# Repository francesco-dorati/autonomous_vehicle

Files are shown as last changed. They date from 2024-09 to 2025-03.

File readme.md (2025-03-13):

# Autonomous Mobile Robot
<!-- [manual interface](./img/manual_interface.png) -->
## Introduction
The aim of this project is to build an autonomous mobile robot capable of **localization**, **mapping** and **autonomous planning** in real-time.
This project is still under development.

### Main Components
- Raspberry Pi 
- Arduino nano
- Arduino RP2040 Connect
- RP Lidar
- [Full components list...](docs/compnents_list.md)

## Software Details
### Program Structure
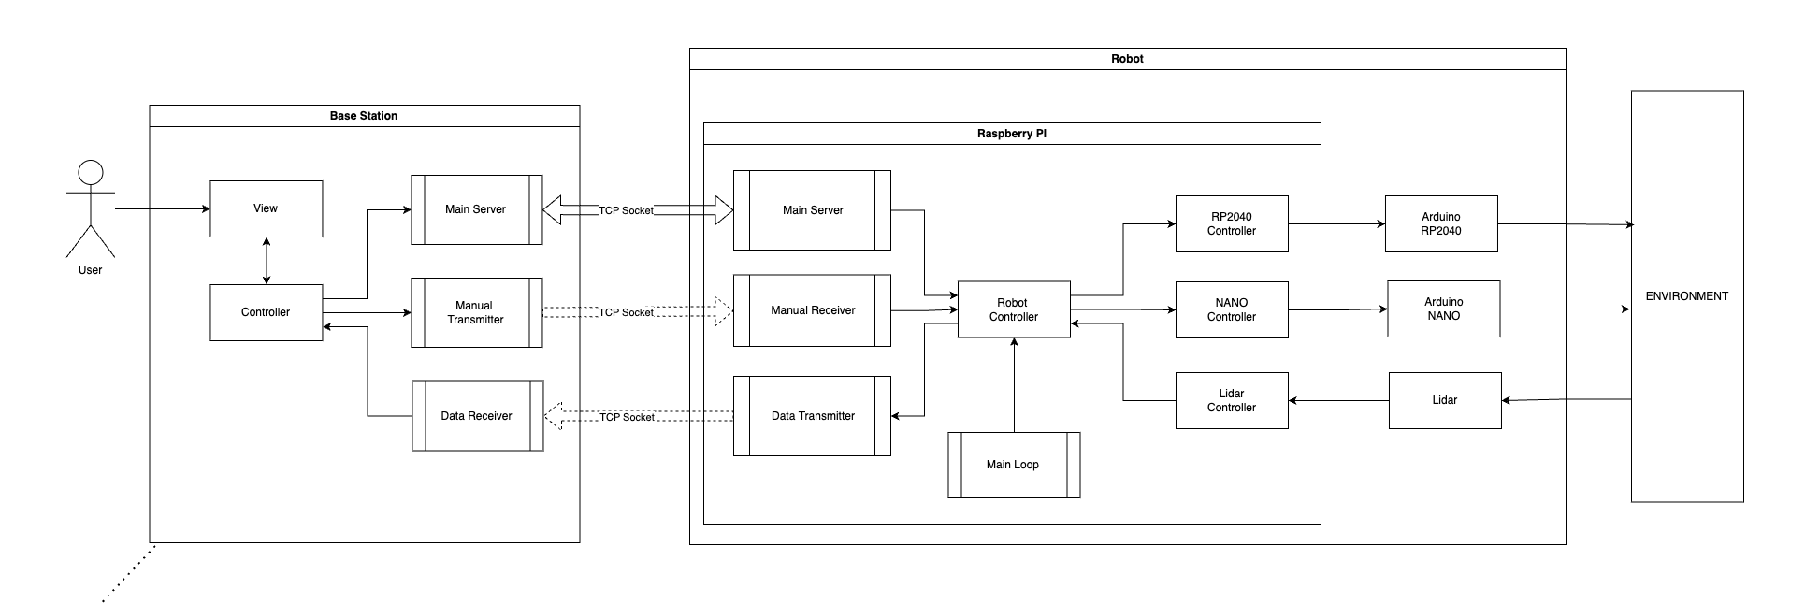
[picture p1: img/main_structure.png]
program structure


#### Robot Controller  (RaspberryPi)
Main controller of the robot, handles main logic and runs the control loop.  

##### Control Loop [4/5 Hz]
The control loop is responsible for the continuous operation of the robot, handling perception, planning, and control tasks.

1. **Perception**
    1. **State Prediction**:
        - Retreaves odometry data from Arduino RP2040
        - Uses an **Extended Kalman Filter (EKF)** to predict the new state (x, y, th, v, w).
    2. **Visual Odometry**:
        - Processes data from the Lidar to create a local map.
        - Uses **ICP** to compute map transformation.
    3. **State Update**:
        - Refines the predicted state using visual odometry data.
    4. **Mapping**:
         - If mapping is enabled, **expands the global map** with lidar data.

2. **Planning**
    1. **Control Commands**: Depending on the control type (position or velocity), sends appropriate commands to the RP2040 to move the robot.

The loop runs continuously at a specified interval, ensuring the robot can navigate and map its environment in real-time.  
[[robot.py](src/raspberry_pi/robot/robot.py)]

#### Motor Controller (Arduino RP2040) [50 Hz]
Handles velocity control of motors and wheel odomtery.
Receives commands from the Robot Controller and translates them into motor actions using a PID control.
Sends encoder data to the Robot Controller each loop.
The Arduino RP2040 communicates with the Raspberry Pi via UART2.
[[arduino code](src/arduino_rp2040/main.ino),  [raspberrypi driver](src/raspberrypi/rp2040.py)]

<!-- #### Motor Controller (Arduino Nano)

[[arduino code](src/nano/main.ino),  [raspberrypi driver](src/raspberrypi/nano.py)]
```
NANO LOOP (50Hz):
- read from serial
- set motor powers
``` -->
#### Developer Console (Client)
Graphical interface to allow the end-user to remotely control the robot while receiving camera streaming and sensors feedback.
Connects to RaspberryPI with multiple socket connections.

<!--
### Interfaces & Connections

#### Sockets (DevConsole <-> RaspberryPI):
- main: TCP (req/res)
- manual: UDP (bidirect)
- camera: UDP (monodirect)
```
MAIN
console (request) ->  raspberrypi (response)
"P"          ->    "P <battery_v>"             // Ping
"M <0/1>"    ->    "OK <manual_port>"          // Manual Start/Stop
"C <0/1>"    ->    "OK <camera_port>"          // Camera Start/Stop
"E"          ->    "OK"                        // Close Connection

MANUAL
console: "<boost> <x> <y>"                   // commands (boost, x, y ∈ [-1,0,1])
raspberrypi: "D <fl> <fr> <rl> <rr>",        // obstacle distance (cm, cm, cm, cm)
             "E <vx> <vt> <x> <y> <theta>",  // encoders odometry (cm/s, deg/s, cm, cm, deg)
``` ->
<- 
#### Serial:
- arduino nano: UART0
- arduino rp2040: UART2 -->

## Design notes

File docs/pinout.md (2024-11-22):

### RASPBERRYPI

### ARDUINO RRP2040
 - TX -> GPIO1 RPI 
 - RX -> GPIO0 RPI 
 - D2 -> IN1  (shifter)
 - D3 -> IN2 (shifter)
 - D4 -> ENA (shifter)
 - D5 -> ENB (shifter)
 - D6 -> IN3 (shifter)
 - D7 -> IN4 (shifter)
 - D8 -> RB Encoder
 - D9 -> RA Encoder
 - D10 -> LB Encoder
 - D11 -> LA Encoder

### ARDUINO NANO
 - TX -> RX RPI (shifter)
 - RX -> TX RPI (shifter)
 - A0 -> Bettery Reader
 - D2 -> FL trig
 - D3 -> FL echo
 - D4 -> FR trig
 - D5 -> FR echo
 - D6 -> RL trig
 - D7 -> RL echo
 - D8 -> RR trig
 - D9 -> RR echo

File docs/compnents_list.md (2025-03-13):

## Components:
### Power:
 - Battery 12v 2200mAh 
 - DCDC Converter 12v-5v 15W 
 - Fuse 7.5A 
 - Power Switch

### Controllers:
 - Raspberry PI
 - Arduino RP2040 Connect
 - Arduino NANO

### Motors:
 - L298N Motor Driver
 - DC Motor 12v 170rpm (x2)
    - current: 60mA free, 450mA load, 1300mA stall 

### Sensors:
 - Slamtec RPLIDAR C1 
 - Ultrasonic Sensor HCSR04 (x4)
 - Digital Camera OV5647, 160° 5MP

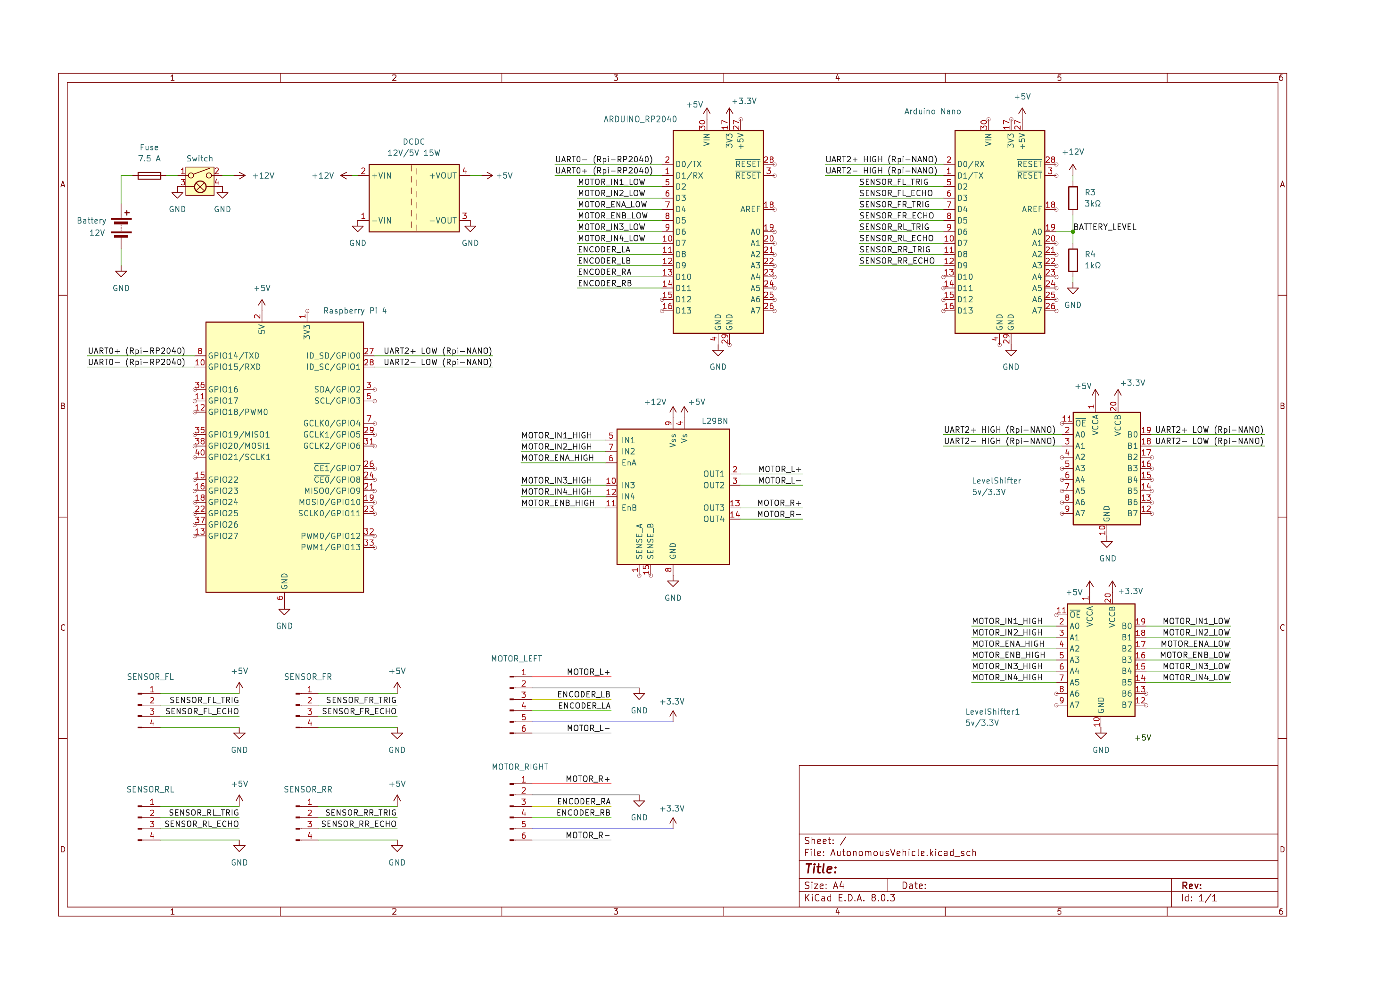
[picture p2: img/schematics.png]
schematics


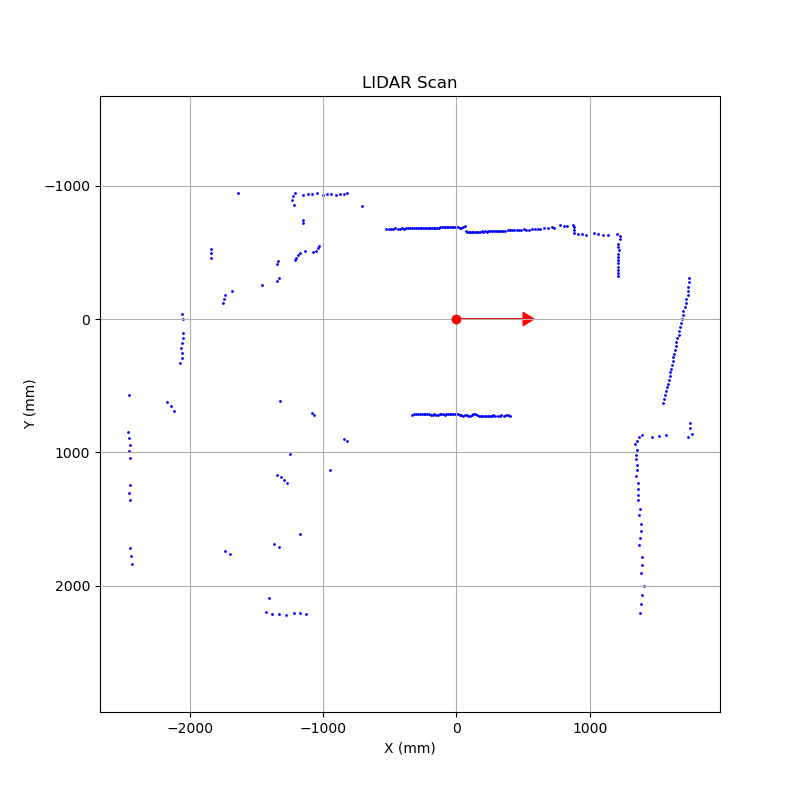
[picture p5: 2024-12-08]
img/local0.png

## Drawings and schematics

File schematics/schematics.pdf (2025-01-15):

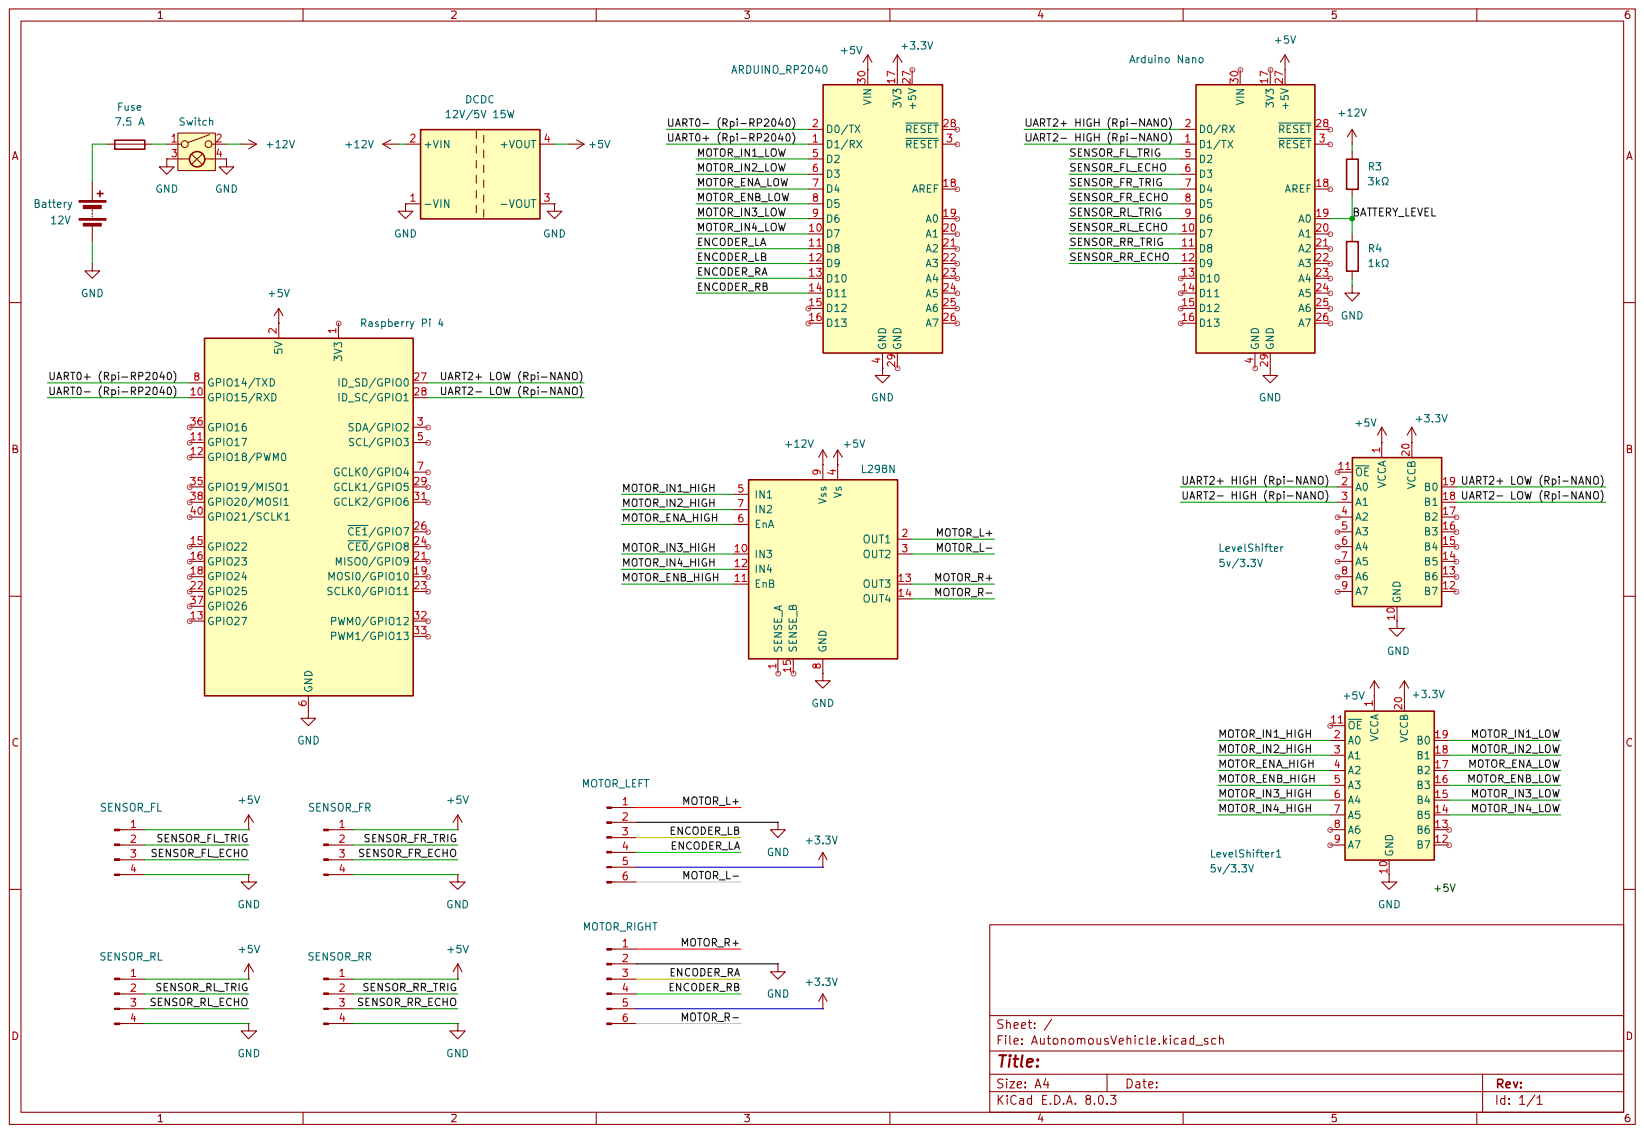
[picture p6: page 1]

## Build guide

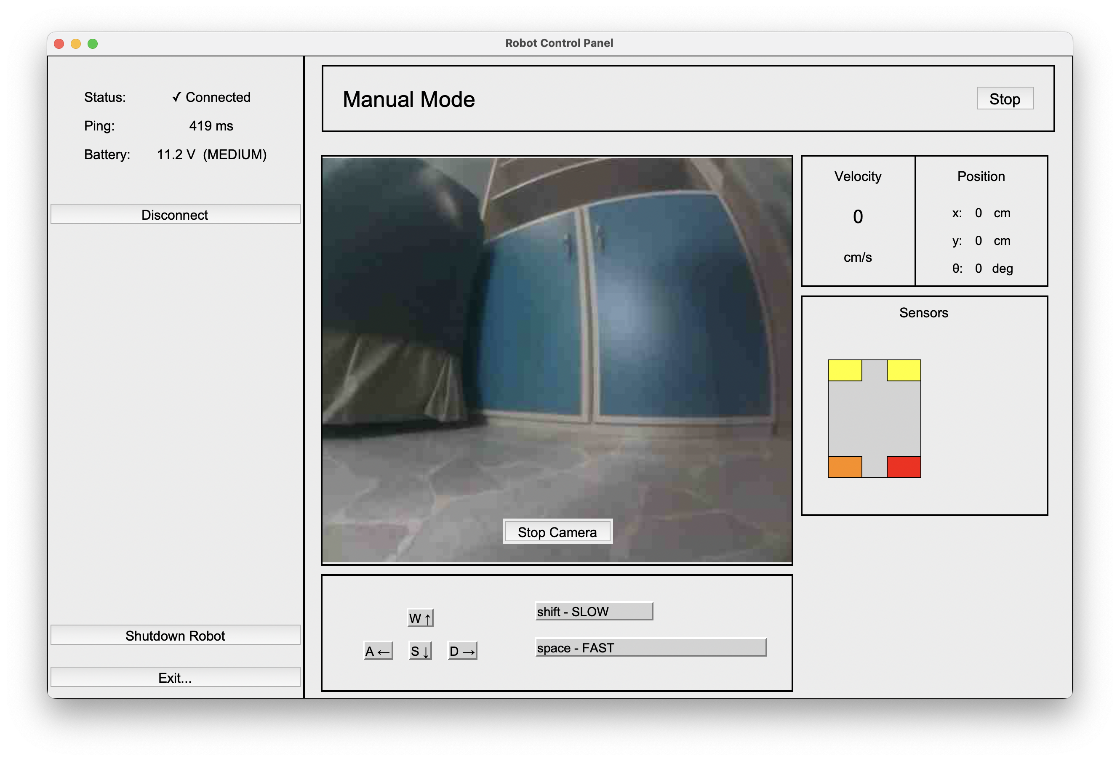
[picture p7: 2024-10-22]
img/manual_interface.png

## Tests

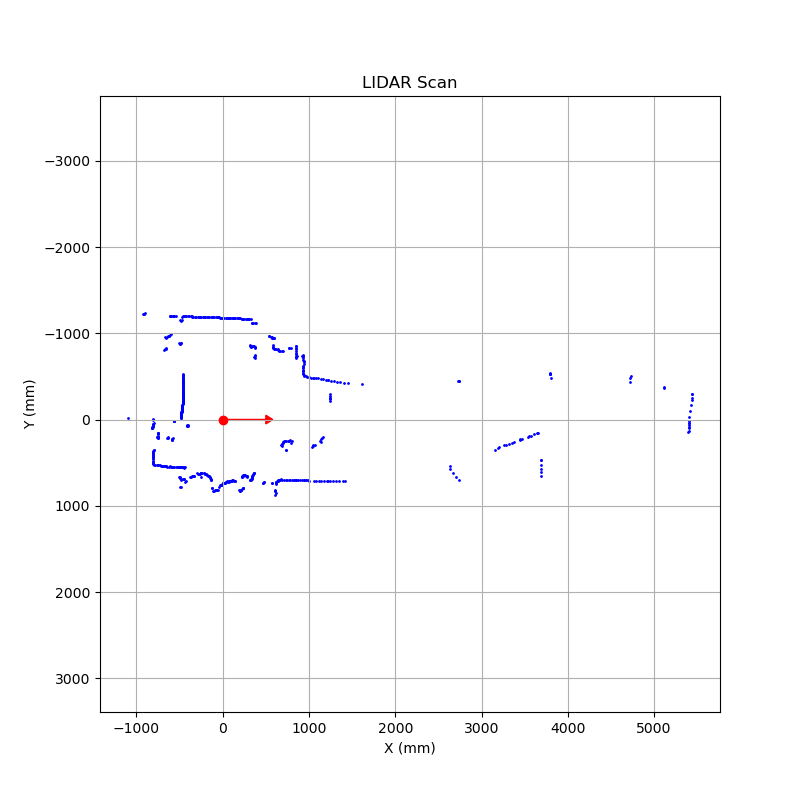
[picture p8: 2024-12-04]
img/test3.png

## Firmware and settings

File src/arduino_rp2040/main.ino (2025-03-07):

#include <Arduino.h>
#include <WiFiNINA.h>
#include <math.h>
#include <PID_v1.h>

/*    
    Motor Controller 
    Handles motor control, path following and encoders odometry calculations
    When not in STALL sends odometry data via serial

    INPUTS (Serial1 115200) 
    ALL INPUTS ENDS WITH '\n'

    "PNG" -> "PNG"
        - ping

    "STP" 
        - stop motors

    "PWR <pow_l> <pow_r>" 
        - set target power
        - (pow_l, pow_r) [int] in [-255, 255]

    "VEL <vx> <vt>" 
        - set target velocity
        - (vx, vt) [int] in [mm/s, mrad/s]

    "PID <kp> <ki> <kd>"
        - change pid values

    "ORS"
        - reset odometry values
    
    "OST <x> <y> <theta>"
        - set odometry values
        - (x, y) in [mm], theta in [mrad]

    "ODB" -> "<x> <y> <theta> <vx> <vy>"
        - get debug odometry values
        - (x, y) in [mm], theta in [mrad], 
        - (vl, va) in [mm/s, mrad/s]

    "PTH <n> <x1> <y1> <th1> ... <xn> <yn> <thn>"
        - set new path to follow
        - n: number of points
        - (x, y) in [mm], th in [mrad]
        - requirements:
            - max number of points simultaneously: 20
            - distance between targets: 100 mm < dist < 1000 mm
            - heading between targets < pi
    
    "APP <n> <x> <y> <th> ... <xn> <yn> <thn>"
        - append point to path
        - n: number of points
        - (x, y) in [mm], th in [mrad]

*/

#define BASE_INTERVAL 20 // ms
#define POSITION_CONTROL_INTERVAL 100 // ms
#define SERIAL_INTERVAL 100 // ms
#define DEBUG_INTERVAL 999 // ms

// STATE
enum State {
    STALL,
    POWER_CONTROL,
    VELOCITY_CONTROL,
    POSITION_CONTROL
};
State control_state = STALL;

// SERIAL
const char END_CHAR = '\n';
long last_serial_time = 0;
void handle_serial();
void transmit_odometry();

// GENERAL
class Position { // general unit
    public:
        int x, y, th;
        Position();
        Position(int x, int y, int th);
        void reset();
};
bool is_over(long last_time, int interval);
void sleep(long t_start);

// ENCODERS
#define LA_ENCODER_PIN 10 // LEFT YELLOW 
#define LB_ENCODER_PIN 11 // LEFT GREEN
#define RA_ENCODER_PIN 9  // RIGHT GREEN
#define RB_ENCODER_PIN 8  // RIGHT YELLOW
#define WHEEL_RADIUS_MM 34      // mm
#define WHEEL_CIRCUMFERENCE_UM 213628   // um  
#define WHEEL_DISTANCE_MM 240   // mm
#define COUNTS_PER_REV 370
#define TWO_PI_URAD 6283185     // 2π in microradians
#define PI_URAD 3141593.6       // π in microradians
#define TWO_PI_MRAD 6283.1853
#define PI_MRAD 3141.5936
volatile long ticks_l, ticks_r;
long prev_ticks_l, prev_ticks_r, prev_time_encoder_us;
int actual_wheel_velocities_m[2]; // vl, vr (mm/s)
int actual_robot_velocities_m[2]; // vx (mm/s), vt (mrad/s)
Position actual_robot_position_u = Position(); // x, y (um), theta (urad)
void left_tick();
void right_tick();
void reset_odometry();
void update_odometry();

// ODOMTERY
long last_odometry_time_us = 0;
long odometry_dtime_us = 0;
long enc_dS_um, enc_dT_urad;
long imu_dT_urad; 

// POWER CONTROL
#define MAX_POW 250
#define MIN_POW 0
#define ENA 4   // BROWN
#define IN1 2   // RED
#define IN2 3   // ORANGE
#define ENB 5   // BLUE
#define IN3 6   // YELLOW
#define IN4 7   // GREEN
int target_powers[2] = {0, 0}; // left, right
void send_motor_powers();
void stop_motors();

// // VELOCITY CONTROL
#define MIN_W_VEL 10 // mm/s
int target_robot_velocities_m[2] = {0, 0}; // vx (mm/s), vt (mrad/s)
int target_wheel_velocities_m[2] = {0, 0}; // vl, vr (mm/s)
double pid_goal_left = 0, pid_goal_right = 0; // PID goal
double pid_actual_left = 0, pid_actual_right = 0; // PID actual
double pid_output_left = 0, pid_output_right = 0; // PID output
double Kp = 1.1, Ki = 3, Kd = 0.004;
PID PID_LEFT(&pid_actual_left, &pid_output_left, &pid_goal_left, Kp, Ki, Kd, DIRECT);
PID PID_RIGHT(&pid_actual_right, &pid_output_right, &pid_goal_right, Kp, Ki, Kd, DIRECT);
void velocity_control();

// POSITION CONTROL
#define QUEUE_SIZE 20
class PositionQueue {
    public:
        PositionQueue();
        Position pop();
        void push(Position p);
        bool is_empty();
        void reset();
    private:
        Position queue[QUEUE_SIZE];
        int front, rear, count;
};
long last_position_control_time = 0;
Position target_robot_position_m = Position(); // x, y (mm), theta (mrad)
PositionQueue target_position_queue = PositionQueue();
void position_control();
void calculate_inverse_kinematic();
// dist
#define THRESH_DIST_MM 50   // mm   distance where target is reached
#define CHANGE_TARGET_DIST_MM 150 // mm    distance where target is changed
#define CHANGE_LIN_SPEED_DIST_MM 130 // mm     distance where maximum speed is reached
#define MIN_LIN_SPEED_MMS 150         // mm/s    minimum speed
#define MAX_LIN_SPEED_MMS 300       // mm/s    maximum speed
int distance_error_mm();
int distance_velocity(int dist_mm);
// heading
#define THRESH_HEAD_MRAD 100 // 5 degrees    angle where target is reached
#define START_HEAD_MRAD 600 
#define CHANGE_ANG_SPEED_HEAD_MRAD 150 // mrad/s  angle where minimum speed is reached
#define MIN_ANG_SPEED_MRADS 400 // mrad/s        minimum speed
#define MAX_ANG_SPEED_MRADS 600 // mrad/s      maximum speed
int heading_error_mrad();
int heading_velocity(int heading_mrad);
// // alpha
#define THRESH_ALIGN_MRAD 20 // 10 degrees
#define VEL_ALIGN_MRADS 470 // 5 degrees
int align_error_mrad();
int align_velocity(int alpha_mrad);

// DEBUG
class Logger { // handle serial inside, check serial to be run every start of turn
    class SerialLogger {
        public:
            bool on;
            void received(char command[]);
            void ping();
            void stop_motors();
            void set_powers();
            void set_velocities();
            void set_pid();
            void request_odometry(int x_mm, int y_mm, int th_mm);
            void reset_odometry();
            void set_odometry();
            void complete_odometry(int x_mm, int y_mm, int th_mm, int v_lin, int v_ang);
            void set_path();
            void append_path();
            void invalid_command();
    };
    class OdometryLogger {
        public:
            bool on;
            bool is_time;
            void log(long ticks_l, long ticks_r, long d_ticks_l, long d_ticks_r, long d_time_us, 
                        long dL_um, long dR_um, long dS_um, long dT_urad);
    };
    class ControlLogger {
        public:
            bool on;
            bool is_time;
            void log_change_target_position(int dist_mm);
            void log_heading_adjustment(int dist_mm, int heading_error);
            void log_alignment_adjustment(int dist_mm, int align_error);
            void log_velocity();
            void log_power();
    };
    
    public:
        SerialLogger serial;
        OdometryLogger odometry;
        ControlLogger control;
        Logger(); // setup serial
        void check_connection();
        
    private:
        bool is_time;
        long last_check_time;

};
Logger debug_usb = Logger();



// SETUP
void setup() {
    Serial.begin(9600);
    Serial1.begin(115200);

    // Left Motor
    pinMode(ENA, OUTPUT);
    pinMode(IN1, OUTPUT);
    pinMode(IN2, OUTPUT);
    // Right Motor
    pinMode(ENB, OUTPUT);
    pinMode(IN3, OUTPUT);
    pinMode(IN4, OUTPUT);

    // Encoders
    pinMode(LA_ENCODER_PIN, INPUT);
    pinMode(LB_ENCODER_PIN, INPUT);
    pinMode(RA_ENCODER_PIN, INPUT);
    pinMode(RB_ENCODER_PIN, INPUT);
    attachInterrupt(digitalPinToInterrupt(RA_ENCODER_PIN), right_tick, RISING);
    attachInterrupt(digitalPinToInterrupt(LA_ENCODER_PIN), left_tick, RISING);

    // PID
    PID_LEFT.SetMode(AUTOMATIC);
    PID_LEFT.SetOutputLimits(-MAX_POW, MAX_POW);
    PID_LEFT.SetSampleTime(BASE_INTERVAL);
    PID_RIGHT.SetMode(AUTOMATIC);
    PID_RIGHT.SetOutputLimits(-MAX_POW, MAX_POW);
    PID_RIGHT.SetSampleTime(BASE_INTERVAL);

    stop_motors();
    reset_odometry();
}


//// LOOP ////
void loop() {
    long t_start = millis();

    // handle serial commands
    if (is_over(last_serial_time, SERIAL_INTERVAL)) {
        // Serial1.write("HEllO!!\n");
        handle_serial();
        last_serial_time = millis();
    } else {
        // check time passed and put stall
    }

    // debug via usb serial
    /* log */ debug_usb.check_connection();  
    
    // stall
    if (control_state == STALL) {
        // stop motors???
        sleep(t_start);
        return;
    }
    
    // update odometry
    update_odometry();
    
    // position control
    if (control_state == POSITION_CONTROL && is_over(last_position_control_time, POSITION_CONTROL_INTERVAL)) {
        // calculate target robot velocities
        position_control(); 
        calculate_inverse_kinematic(); // calculate target wheels velocity
        last_position_control_time = millis();
    }

    // velocity control
    if (control_state == POSITION_CONTROL || control_state == VELOCITY_CONTROL) {
        // compute motor powers
        velocity_control();
    }

    if (target_powers[0] == 0 && target_powers[1] == 0) { stop_motors(); }

    // send motor powers
    send_motor_powers();

    // transmit odometry
    transmit_odometry();
    
    // delay
    sleep(t_start);
    
}

bool is_over(long last_time, int interval) {
    return (millis() - last_time) >= interval;
}
void sleep(long t_start) {
    int dt = millis() - t_start;
    if (dt < BASE_INTERVAL) 
        delay(BASE_INTERVAL - dt);
}

void stop_motors() {
    control_state = STALL;
    target_powers[0] = 0;
    target_powers[1] = 0;
    send_motor_powers();
    target_robot_velocities_m[0] = 0;
    target_robot_velocities_m[1] = 0;
    target_robot_position_m.reset();
    target_position_queue.reset();
}

long normalize_angle_urad(long angle) {
    return ((angle + (int) PI_URAD) % (int) TWO_PI_URAD) - PI_URAD;
}
long normalize_angle_mrad(long angle) {
    return ((angle + (int) PI_MRAD) % (int) TWO_PI_MRAD) - PI_MRAD;
}

Position::Position() {
    this->x = 0;
    this->y = 0;
    this->th = 0;
}
Position::Position(int x, int y, int th) {
    this->x = x;
    this->y = y;
    this->th = th;
}
void Position::reset() {
    this->x = 0;
    this->y = 0;
    this->th = 0;
}

// SERIAL
void handle_serial() {
    while (Serial1.available() >= 3) {
        char command[4];
        command[3] = '\0';

        Serial1.readBytes(command, 3);
        /* log */ debug_usb.serial.received(command); 

        if (strcmp(command, "PNG") == 0) {
            // ping
            Serial1.println("PNG");
            /* log */ debug_usb.serial.ping();

        } else if (strcmp(command, "STP") == 0) {
            // stop motors
            // "STP"
            stop_motors();
            /* log */ debug_usb.serial.stop_motors();

        } else if (strcmp(command, "PWR") == 0) {
            // power control
            // "PWR <pow_l> <pow_r>" 
            // if (Serial1.available() < 2) return;
            target_powers[0] = Serial1.parseInt();
            target_powers[1] = Serial1.parseInt();
            control_state = POWER_CONTROL;
            /* log */ debug_usb.serial.set_powers();

        } else if (strcmp(command, "VEL") == 0) {
            // velocity control
            // "VEL <vx> <vt>" 
            // if (Serial1.available() < 3) return;
            target_robot_velocities_m[0] = Serial1.parseInt();
            target_robot_velocities_m[1] = Serial1.parseInt();
            calculate_inverse_kinematic();
            control_state = VELOCITY_CONTROL;
            /* log */ debug_usb.serial.set_velocities();

        } else if (strcmp(command, "PID") == 0) {
            // pid values change
            // "PID <kp> <ki> <kd>"
            // if (Serial1.available() < 6) return;
            Kp = Serial1.parseFloat();
            Ki = Serial1.parseFloat();
            Kd = Serial1.parseFloat();
            PID_LEFT.SetTunings(Kp, Ki, Kd);
            PID_RIGHT.SetTunings(Kp, Ki, Kd);
            /* log */ debug_usb.serial.set_pid();

        } else if (strcmp(command, "ORS") == 0) {
            // odometry reset
            // "ORS"
            reset_odometry();
            /* log */ debug_usb.serial.reset_odometry();

        } else if (strcmp(command, "OST") == 0) {
            // odometry set
            // "OST <x> <y> <theta>"
            int x_u = Serial1.parseInt()*1000; 
            int y_u = Serial1.parseInt()*1000; 
            int th_u = Serial1.parseInt()*1000; 
            actual_robot_position_u = Position(x_u, y_u, th_u);
            /* log */ debug_usb.serial.set_odometry();

        } else if (strcmp(command, "ODB") == 0) {
            // odometry debug
            // "ORQ" -> "<x> <y> <theta> <vl> <va>"
            int x_mm = actual_robot_position_u.x/1000;
            int y_mm = actual_robot_position_u.y/1000;
            int th_mm = actual_robot_position_u.th/1000;
            int v_lin = actual_robot_velocities_m[0];
            int v_ang = actual_robot_velocities_m[1];
            Serial1.print(x_mm); // x
            Serial1.print(" ");
            Serial1.print(y_mm); // y
            Serial1.print(" ");
            Serial1.print(th_mm); // theta
            Serial1.print(" ");
            Serial1.print(v_lin); // vx
            Serial1.print(" ");
            Serial1.println(v_ang); // vt
            /* log */ debug_usb.serial.complete_odometry(x_mm, y_mm, th_mm, v_lin, v_ang);

        } else if (strcmp(command, "PTH") == 0) {
            // set path to follow
            // "PTH <n> <x1> <y1> <th1> ... <xn> <yn> <thn>"
            target_position_queue.reset();
            int n = Serial1.parseInt();
            for (int i = 0; i < n; i++) {
                long x_mm = Serial1.parseInt();
                long y_mm = Serial1.parseInt();
                long th_mrad = Serial1.parseInt();
                target_position_queue.push(Position(x_mm, y_mm, th_mrad));
            }
            control_state = POSITION_CONTROL;
            /* log */ debug_usb.serial.set_path();

        } else if (strcmp(command, "APP") == 0) {
            int n = Serial1.parseInt();
            for (int i = 0; i < n; i++) {
                long x_mm = Serial1.parseInt();
                long y_mm = Serial1.parseInt();
                long th_mrad = Serial1.parseInt();
                target_position_queue.push(Position(x_mm, y_mm, th_mrad));
            }
            control_state = POSITION_CONTROL;
            /* log */ debug_usb.serial.append_path();

        } else {
            // invalid command
            // ignore
            /* log */ debug_usb.serial.invalid_command();
        }

        // read until END
        while (Serial1.available() > 0 && Serial1.read() != END_CHAR) {};
    }
}

void transmit_odometry() {
    // "T <time> ENC <ticks_l> <ticks_r> <d_ticks_l> <d_ticks_r> <d_time_us> <dL_um> <dR_um> <dS_um> <dT_urad>"
    String message = "";
    message += "T:";
    message += String(odometry_dtime_us);
    message += ";ENC:";
    message += String(enc_dS_um);
    message += ",";
    message += String(enc_dT_urad);
    message += ";IMU: ";
    // message += String(imu_dT_urad);
    Serial1.println(message);
}

// ODOMETRY
void left_tick() { 
    if (digitalRead(LB_ENCODER_PIN) == HIGH) ticks_l++;  // Forward
    else ticks_l--;  // Backward
}
void right_tick() {
    if (digitalRead(RB_ENCODER_PIN) == HIGH) ticks_r++;  // Forward
    else ticks_r--;  // Backward
} 
void reset_odometry() {
    ticks_l = 0;
    ticks_r = 0;
    prev_ticks_l = 0;
    prev_ticks_r = 0;
    prev_time_encoder_us = micros();
    enc_dS_um = 0;
    enc_dT_urad = 0;
    actual_wheel_velocities_m[0] = 0;
    actual_wheel_velocities_m[1] = 0;
    actual_robot_velocities_m[0] = 0; 
    actual_robot_velocities_m[1] = 0;
    actual_robot_position_u.reset();
    target_robot_position_m.reset();
    target_position_queue.reset();
}
void update_odometry() {
    /*
        Updates the robot odometry
        reads: ticks_l, ticks_r
        writes: actual_wheel_velocities_m[2], actual_robot_velocities_m[2], actual_robot_position_u[3]
    */
    // calcola delta time
    if (last_odometry_time_us != 0)
        odometry_dtime_us = micros() - last_odometry_time_us;
    last_odometry_time_us = micros();

    // delta ticks
    long d_ticks_l = ticks_l - prev_ticks_l;
    long d_ticks_r = ticks_r - prev_ticks_r;
    prev_ticks_l = ticks_l;
    prev_ticks_r = ticks_r;

    // delta time
    long t_us = micros();
    float d_time_us = (t_us - prev_time_encoder_us);
    prev_time_encoder_us = t_us;

    long dL_um = (d_ticks_l * WHEEL_CIRCUMFERENCE_UM) / COUNTS_PER_REV;
    long dR_um = (d_ticks_r * WHEEL_CIRCUMFERENCE_UM) / COUNTS_PER_REV;

    enc_dS_um = (dL_um + dR_um) / 2; // um
    enc_dT_urad = (dR_um - dL_um) * 1000 / WHEEL_DISTANCE_MM; // urad

    // wheel velocities
    // (um*1000)/us = nm/us = mm/s
    actual_wheel_velocities_m[0] = (dL_um * 1000) / d_time_us; 
    actual_wheel_velocities_m[1] = (dR_um * 1000) / d_time_us;

    // robot velocities
    // (um*1000)/us = nm/us = mm/s
    actual_robot_velocities_m[0] = (enc_dS_um * 1000)/ d_time_us; 
    actual_robot_velocities_m[1] = (enc_dT_urad * 1000) / d_time_us;


    // robot position
    // actual_robot_position_u.x += dS_um * cos(actual_robot_position_u.th/1000000.0); // um
    // actual_robot_position_u.y += dS_um * sin(actual_robot_position_u.th/1000000.0); // um
    actual_robot_position_u.x += enc_dS_um * cos((actual_robot_position_u.th + enc_dT_urad/2)/1000000.0); // um
    actual_robot_position_u.y += enc_dS_um * sin((actual_robot_position_u.th + enc_dT_urad/2)/1000000.0); // um
    actual_robot_position_u.th += enc_dT_urad; // urad
    actual_robot_position_u.th = normalize_angle_urad(actual_robot_position_u.th);


    //DEBUG
    /* log */ debug_usb.odometry.log(ticks_l, ticks_r, d_ticks_l, d_ticks_r, d_time_us, 
                                                    dL_um, dR_um, enc_dS_um, enc_dT_urad);
}

// POWER CONTROL
void send_motor_powers() {
    /*  
        Sends the motor powers to the motors
        target_powers[0] -> left motor [-255, 255]
        target_powers[1] -> right motor [-255, 255]
    */

    // saturation
    // left
    if (abs(target_powers[0]) > MAX_POW) target_powers[0] = (target_powers[0] > 0) ? MAX_POW : -MAX_POW;
    if (abs(target_powers[0]) < MIN_POW) target_powers[0] = 0;
    // right
    if (abs(target_powers[1]) > MAX_POW) target_powers[1] = (target_powers[1] > 0) ? MAX_POW : -MAX_POW;
    if (abs(target_powers[1]) < MIN_POW) target_powers[1] = 0;

    // update motors
    // left
    if (target_powers[0] == 0){
        analogWrite(ENB, 0);
        digitalWrite(IN3, LOW);
        digitalWrite(IN4, LOW);
    } else {
        analogWrite(ENB, abs(target_powers[0]));
        digitalWrite(IN3, (target_powers[0] > 0) ? LOW : HIGH);
        digitalWrite(IN4, (target_powers[0] > 0) ? HIGH : LOW);
    }
    // right
    if (target_powers[1] == 0){
        analogWrite(ENA, 0);
        digitalWrite(IN1, LOW);
        digitalWrite(IN2, LOW);
    } else{
        analogWrite(ENA, abs(target_powers[1]));
        digitalWrite(IN1, (target_powers[1] > 0) ? LOW : HIGH);
        digitalWrite(IN2, (target_powers[1] > 0) ? HIGH : LOW);
    }

    /* log */ debug_usb.control.log_power();
}

// VELOCITY CONTROL
void velocity_control() {
    /*
        Computes the motor powers based on the target velocities
        (wheels velocities are already calculated)
        reads: target_wheel_velocities_m[2]
        writes: target_powers[2] 
    */   
   // update pid variables 
   pid_actual_left = actual_wheel_velocities_m[0];
   pid_actual_right = actual_wheel_velocities_m[1];
   pid_goal_left = target_wheel_velocities_m[0];
   pid_goal_right = target_wheel_velocities_m[1];
   
   // floor small velocities
    if (abs(pid_goal_left) < MIN_W_VEL && abs(pid_goal_right) < MIN_W_VEL) {
        stop_motors();
        return;
    }

    // compute PID
    PID_LEFT.Compute();
    PID_RIGHT.Compute();
    // update target powers
    target_powers[0] = (int) max(-255, min(pid_output_left, 255));
    target_powers[1] = (int) max(-255, min(pid_output_right, 255));

    /* log */ debug_usb.control.log_velocity();
}

// POSITION CONTROL
PositionQueue::PositionQueue() { 
    front = 0; rear = 0; count = 0;
}
Position PositionQueue::pop() {
    /*
        Returns the next point to follow
        requires: !is_empty()
    */
    if (this->is_empty()) return Position();
    Position p = queue[front];
    front = (front + 1) % QUEUE_SIZE;
    count--;
    return p;
}
void PositionQueue::push(Position p) {
    /*
        Adds a new point to the queue
        requires: count < QUEUE_SIZE
    */
    if (count == QUEUE_SIZE) return;
    queue[rear] = p;
    rear = (rear + 1) % QUEUE_SIZE;
    count++;
}
bool PositionQueue::is_empty() {
    return count == 0;
}
void PositionQueue::reset() {
    front = 0; rear = 0; count = 0;
}
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

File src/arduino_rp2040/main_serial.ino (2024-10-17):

#include <Arduino.h>
#include <Wire.h>
#include <WiFiNINA.h>
#include <math.h>

#define LOOP_DELAY_MS 20 // ms
#define BATTERY_DELAY_MS 1000 // ms

#define FL_trig 2
#define FL_echo 3
#define FR_trig 4
#define FR_echo 5
#define RL_trig 6
#define RL_echo 7
#define RR_trig 8
#define RR_echo 9
#define LA_encoder 10
#define LB_encoder 11
#define RA_encoder A1
#define RB_encoder A2
#define battery_reader A0

#define wheel_radius_mm 34 // mm
#define wheel_distance_mm 240 // mm
#define counts_per_rev 370
#define half_sound_speed_mm_us 0.1715 // mm/us
#define TWO_PI_URAD 6283185   // 2π in microradians
#define PI_URAD 3141593.6       // π in microradians
#define PI_MRAD 3141.5936

const long wheel_circumference_mm = 2*PI*wheel_radius_mm;

int battery_voltage_mv = 0; // millivolts
int dist_mm[4] = {0, 0, 0, 0}; // FL FR RL RR (mm)
int wheel_velocities[2] = {0, 0}; // vl, vr (mm/s)
int robot_velocities[2] = {0, 0}; // vx (mm/s), vt (mrad/s)
long robot_position[3] = {0, 0, 0}; // x, y (um), theta (urad)

bool battery_reader_running = true;
bool distance_running = false;
bool encoders_running = false;

long last_battery_time = 0;


// sensor
int sensor_n = 0; // fl, rl, fr, rr
// encoder
volatile long ticks_l, ticks_r;
long prev_ticks_l, prev_ticks_r, prev_time_encoder_us;

void left_tick();
void right_tick();
void update_encoders();

void update_battery();
void update_sensors();
int get_distance_mm(uint8_t trig, uint8_t echo);

void setup() {
    // serial
    Serial.begin(9600);
    Serial1.begin(115200);

    // sensors
    pinMode(FL_trig, OUTPUT);
    pinMode(FL_echo, INPUT);
    pinMode(FR_trig, OUTPUT);
    pinMode(FR_echo, INPUT);
    pinMode(RL_trig, OUTPUT);
    pinMode(RL_echo, INPUT);
    pinMode(RR_trig, OUTPUT);
    pinMode(RR_echo, INPUT);

    // encoders
    pinMode(LA_encoder, INPUT);
    pinMode(LB_encoder, INPUT);
    pinMode(RA_encoder, INPUT);
    pinMode(RB_encoder, INPUT);
    attachInterrupt(digitalPinToInterrupt(RA_encoder), right_tick, RISING);
    attachInterrupt(digitalPinToInterrupt(LA_encoder), left_tick, RISING);

    // battery reader
    pinMode(battery_reader, INPUT);
}

void loop() {
    unsigned long t_start = millis();

    // check serial
    if (Serial1.available() > 0) {
        char c = Serial1.read();
        if (c == 'R') // request
            handle_request();
        else if (c == 'S') // set
            handle_set();
    }

    // read battery
    if (battery_reader_running && (millis() - last_battery_time) >= BATTERY_DELAY_MS) 
        update_battery();

    // read sensors
    if (distance_running) 
        update_distance();

    // read encoders
    if (encoders_running) 
        update_encoders();
    
    // delay
    int dt = millis() - t_start;
    // if (Serial) {
    //     Serial.print("LOOP END, time: ");
    //     Serial.print(dt);
    //     Serial.println(" ms");
    // }
    if (dt < LOOP_DELAY_MS)
        delay(LOOP_DELAY_MS - dt);
}

void handle_request() {
    long t = millis();
    Serial1.read();
    if (Serial) Serial.println("REQUEST START");
    
    // BATTERY
    Serial1.print("B ");
    if (battery_reader_running) {
        Serial1.print("1 ");
        Serial1.println(battery_voltage_mv/1000.0); // V
    } else {
        Serial1.println("0");
    }

    // DISTANCE
    Serial1.print("D ");
    if (distance_running) {
        Serial1.print("1 ");
        Serial1.print(dist_mm[0]/10.0); // cm
        Serial1.print(" ");
        Serial1.print(dist_mm[1]/10.0); // cm
        Serial1.print(" ");
        Serial1.print(dist_mm[2]/10.0); // cm
        Serial1.print(" ");
        Serial1.println(dist_mm[3]/10.0); // cm
    } else {
        Serial1.println("0");
    }

    // ENCODER ODOMETRY
    Serial1.print("E ");
    if (encoders_running) {
        Serial1.print("1 ");
        Serial1.print(robot_velocities[0]/10.0); // cm/s
        Serial1.print(" ");
        Serial1.print((robot_velocities[1]*180)/(PI_MRAD)); // rad/s
        Serial1.print(" ");
        Serial1.print(robot_position[0]/10000.0); // cm
        Serial1.print(" ");
        Serial1.print(robot_position[1]/10000.0); // cm
        Serial1.print(" ");
        Serial1.println((robot_position[2]*180)/(PI_URAD)); // deg
    } else {
        Serial1.println("0");
    }

    if (Serial) {
        int dt = millis() - t;
        Serial.print("REQUEST END ");
        Serial.print(dt);
        Serial.println(" ms");
    }

}

void handle_set() {
    if (Serial) Serial.println("SET START");
    char type = Serial1.read();
    char on = Serial1.read() == '1';
    if (type == 'B') {
        battery_reader_running = on;
        reset_battery();
    } else if (type == 'D') {
        distance_running = on;
        reset_distance();
    } else if (type == 'E') {
        encoders_running = on;
        reset_encoders();
    }
    if (Serial) Serial.println("SET END");
}

void reset_battery() {
    battery_voltage_mv = 0;
}

void reset_distance() {
    dist_mm[0] = 0;
    dist_mm[1] = 0;
    dist_mm[2] = 0;
    dist_mm[3] = 0;
}

void reset_encoders() {
    ticks_l = 0;
    ticks_r = 0;
    prev_ticks_l = 0;
    prev_ticks_r = 0;
    prev_time_encoder_us = micros();
    wheel_velocities[0] = 0;
    wheel_velocities[1] = 0;
    robot_velocities[0] = 0; 
    robot_velocities[1] = 0;
    robot_position[0] = 0; 
    robot_position[1] = 0;
    robot_position[2] = 0;
}


void left_tick() { 
    if (!encoders_running) return;
    if (digitalRead(LB_encoder) == HIGH) {
        ticks_l++;  // Forward
    } else {
        ticks_l--;  // Backward
    }
}

void right_tick() {
    if (!encoders_running) return;
    if (digitalRead(RB_encoder) == HIGH) {
        ticks_r++;  // Forward
    } else {
        ticks_r--;  // Backward
    }
} 

void update_battery() {
    // Serial.println("BATTERY START");
    int pin_voltage_mv = (analogRead(battery_reader) / 1023.0) * 3300;
    battery_voltage_mv = pin_voltage_mv * 4;
}
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

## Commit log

2024-05-10 Arduino Base Controller
    [robot.urdf.xacro]
2024-05-15 Implemente PID
2024-05-22 socket server
2024-05-26 create pid
2024-06-20 fix arduino
2024-06-21 adjust PID values
2024-07-03 camera updates
2024-09-23 correct motor pins
2024-09-23 arduino debugging
2024-09-24 fox motor direction
2024-09-28 sensor imporove
2024-09-29 update encoders
2024-09-29 fix encoders
2024-09-29 update arduino
2024-10-05 Fix I2C block data read issue in RP2040 class
    [rp2040.py]
2024-10-06 chore: Disable battery, encoder, and distance commands in RP2040_SER class
2024-10-06 Disable battery, encoder, and distance commands in RP2040_SER class
2024-10-08 chore: Update serial port configuration for RP2040 board
2024-10-11 setup camera
2024-10-11 minor fix camera
2024-10-11 camera fix
2024-10-15 fix camera
2024-10-16 change powers
2024-10-17 update schematics
    [MainScheme.kicad_sch]
2024-10-24 create lidar class
2024-10-24 test lidar
2024-10-26 print scan
2024-10-27 drwa lidar
2024-11-21 create motor controller
2024-11-22 final motor controller
2024-12-04 lidar test
2024-12-04 fix lidar test
2024-12-04 fix lidar
2024-12-06 lidar final
2025-01-15 add logger
    [AutonomousVehicle.kicad_sch]
2025-01-15 updated pid values
2025-01-16 pid testing
2025-01-17 fixed lidar
2025-03-07 updated arduino
2025-03-08 tested odometry
2025-03-08 posibilità di routare local map
2025-03-12 odometry display e autonomous control
2025-03-13 addes schematics image
2025-03-13 add schematics image
